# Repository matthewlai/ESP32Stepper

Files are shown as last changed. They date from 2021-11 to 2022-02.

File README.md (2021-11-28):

# ESP32Stepper

This is the PCB design and firmware for a Trinamic TMC2590-based stepper motor driver with an ESP32 microcontroller.

## Firmware Instructions

The firmware is Arduino based, using the arduino-esp32 port by Espressif.

1. Install the official Arduino IDE from [https://www.arduino.cc/en/software](https://www.arduino.cc/en/software).
2. [Install the ESP32 core](https://docs.espressif.com/projects/arduino-esp32/en/latest/installing.html) (either stable or development branch, using Board Manager).
3. Install the required libraries (see below) using Arduino library manager.
4. Clone this repository, and open ESP32Stepper/firmware/main/main.ino in the Arduino IDE.
5. In Tools, use the following settings:
    * Board: ESP32 Dev Module
    * Port: serial port for the board
    * All other settings as default (240 MHz CPU, 80 MHz flash, QIO, 4MB flash, default 4MB partition scheme, no PSRAM)

## Customisation

1. Set motor-specific parameters in config.h

## Required Libraries

1. Adafruit Neopixel 1.10.0x

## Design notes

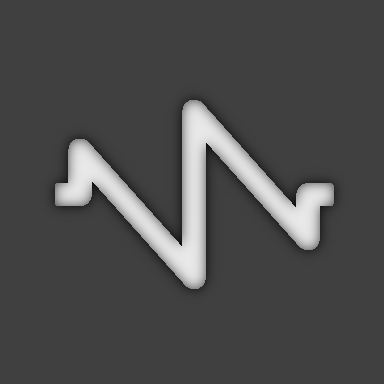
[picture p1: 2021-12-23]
controller/Woodpecker/qml/images/patterns/sawtooth.png

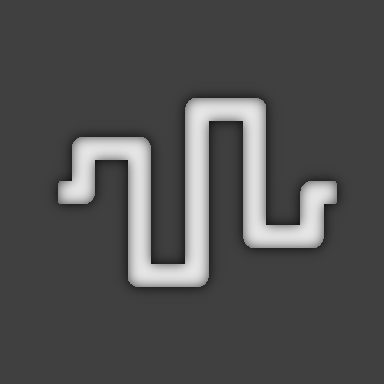
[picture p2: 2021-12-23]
controller/Woodpecker/qml/images/patterns/square.png

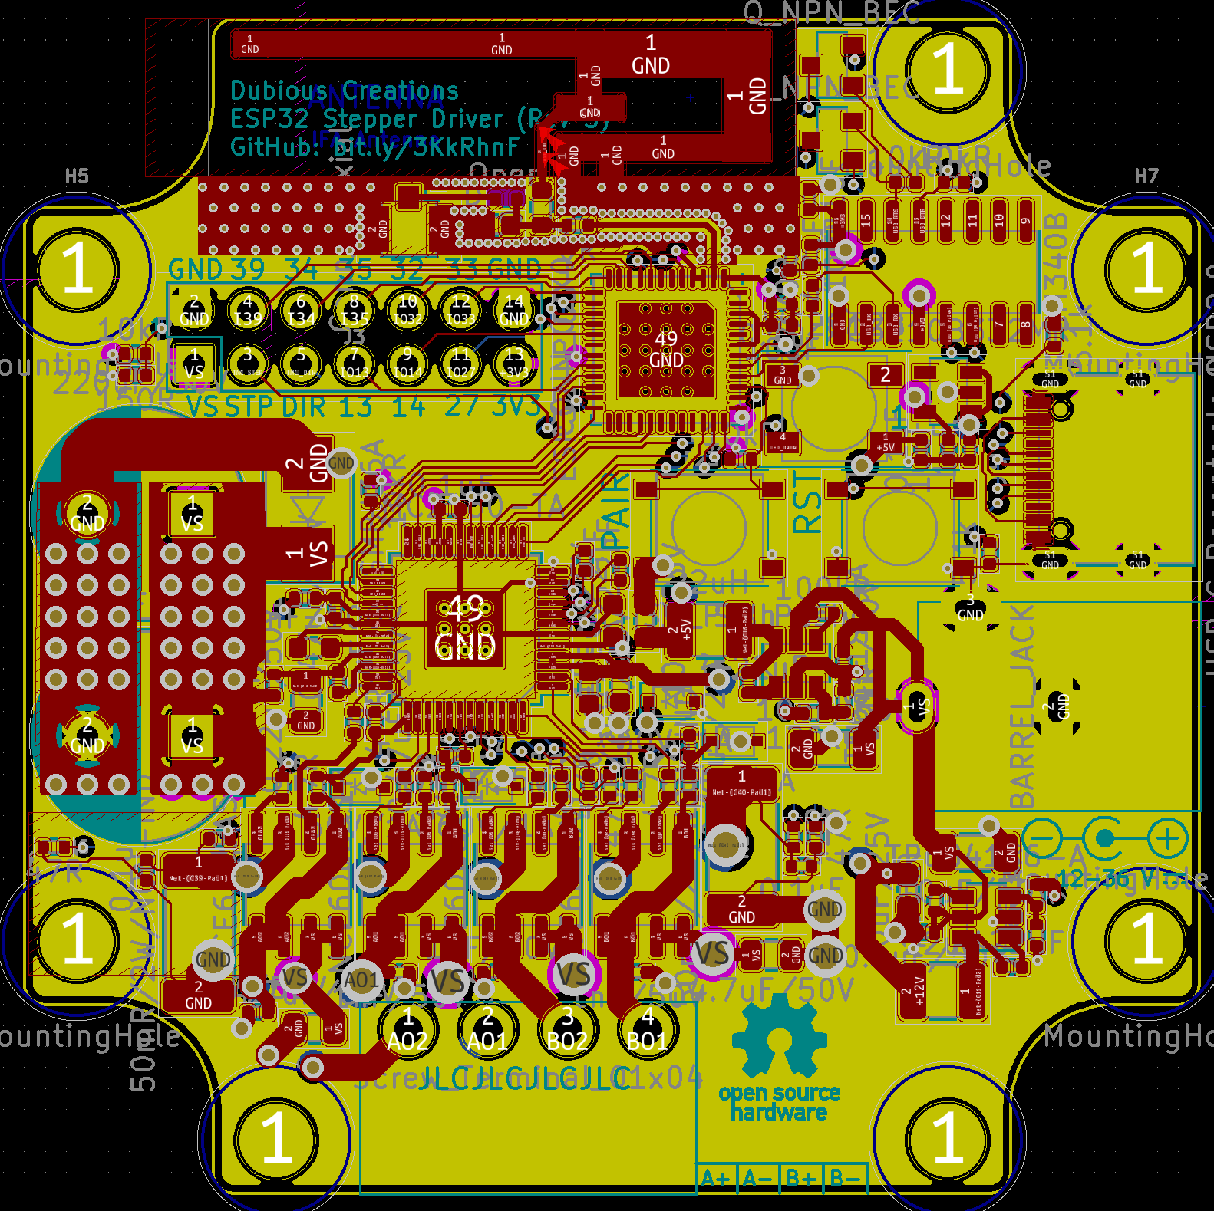
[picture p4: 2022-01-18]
doc/rev3/front.png

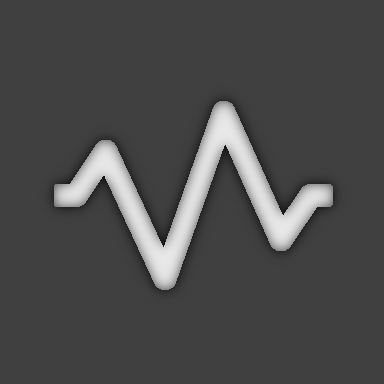
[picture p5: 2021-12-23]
controller/Woodpecker/qml/images/patterns/triangle.png

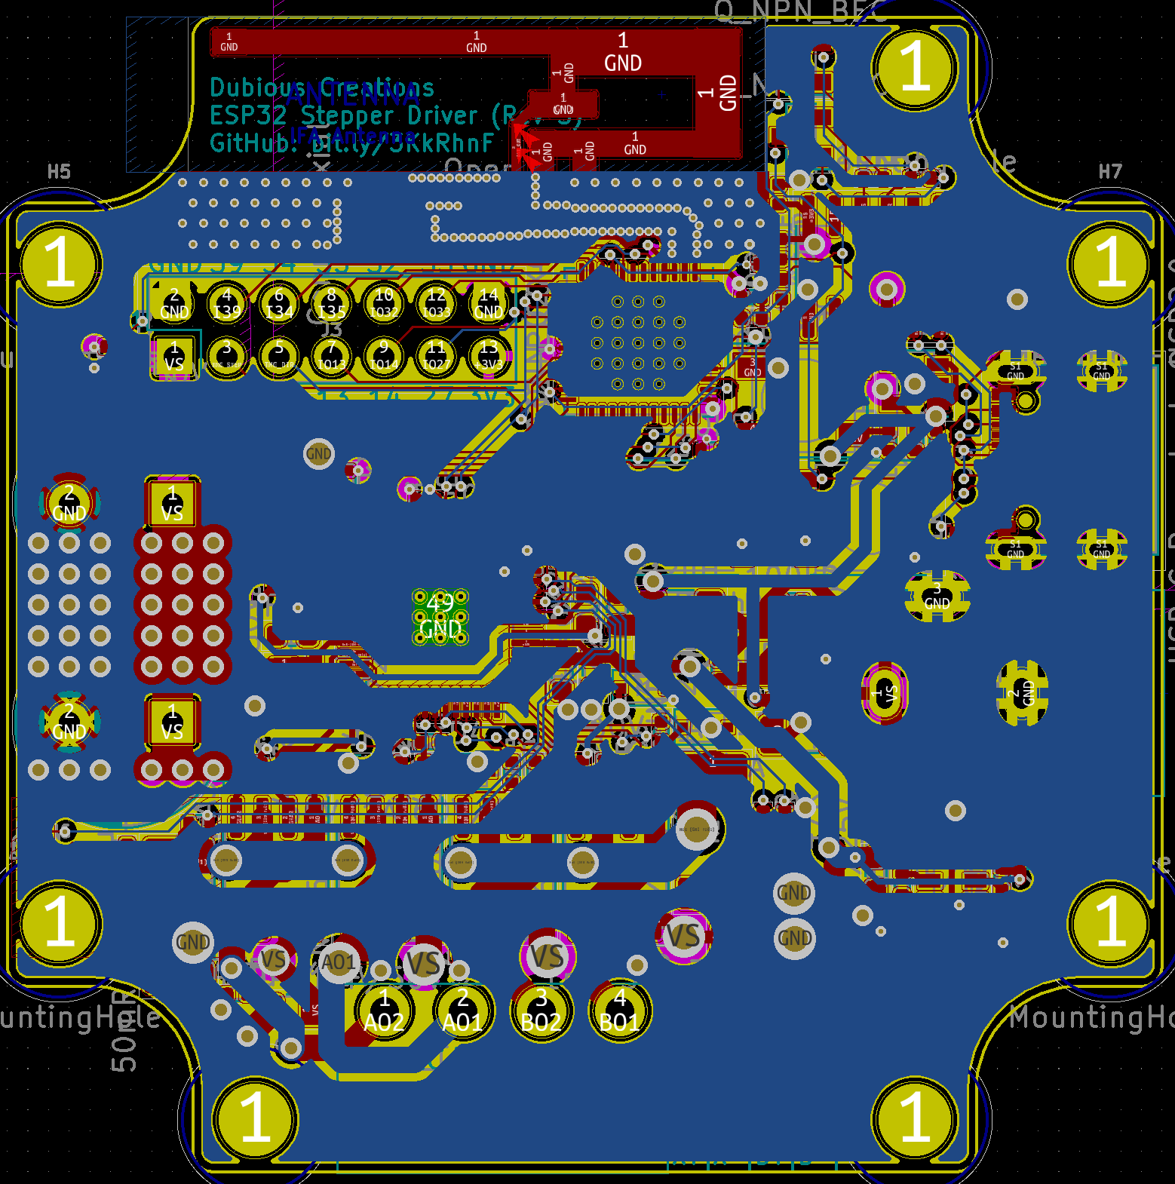
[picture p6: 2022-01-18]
doc/rev3/back.png

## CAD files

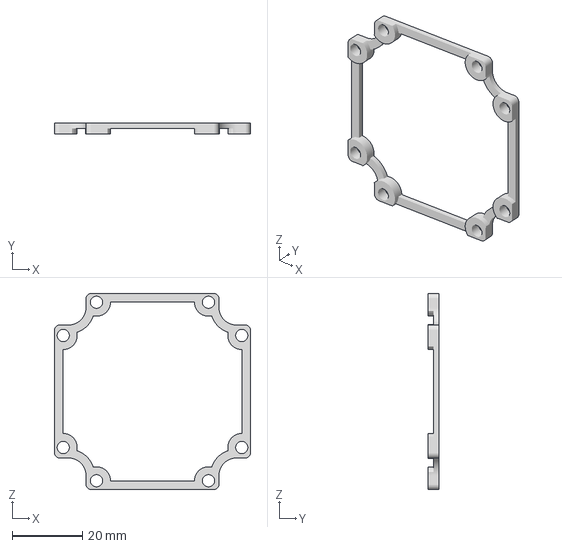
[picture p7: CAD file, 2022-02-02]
mechanical/NEMA23_Stepper_Spacer/stepper_spacer.3mf
56.0 x 3.00 x 56.0 mm

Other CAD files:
mechanical/NEMA23_Stepper_Spacer/stepper_spacer.f3d

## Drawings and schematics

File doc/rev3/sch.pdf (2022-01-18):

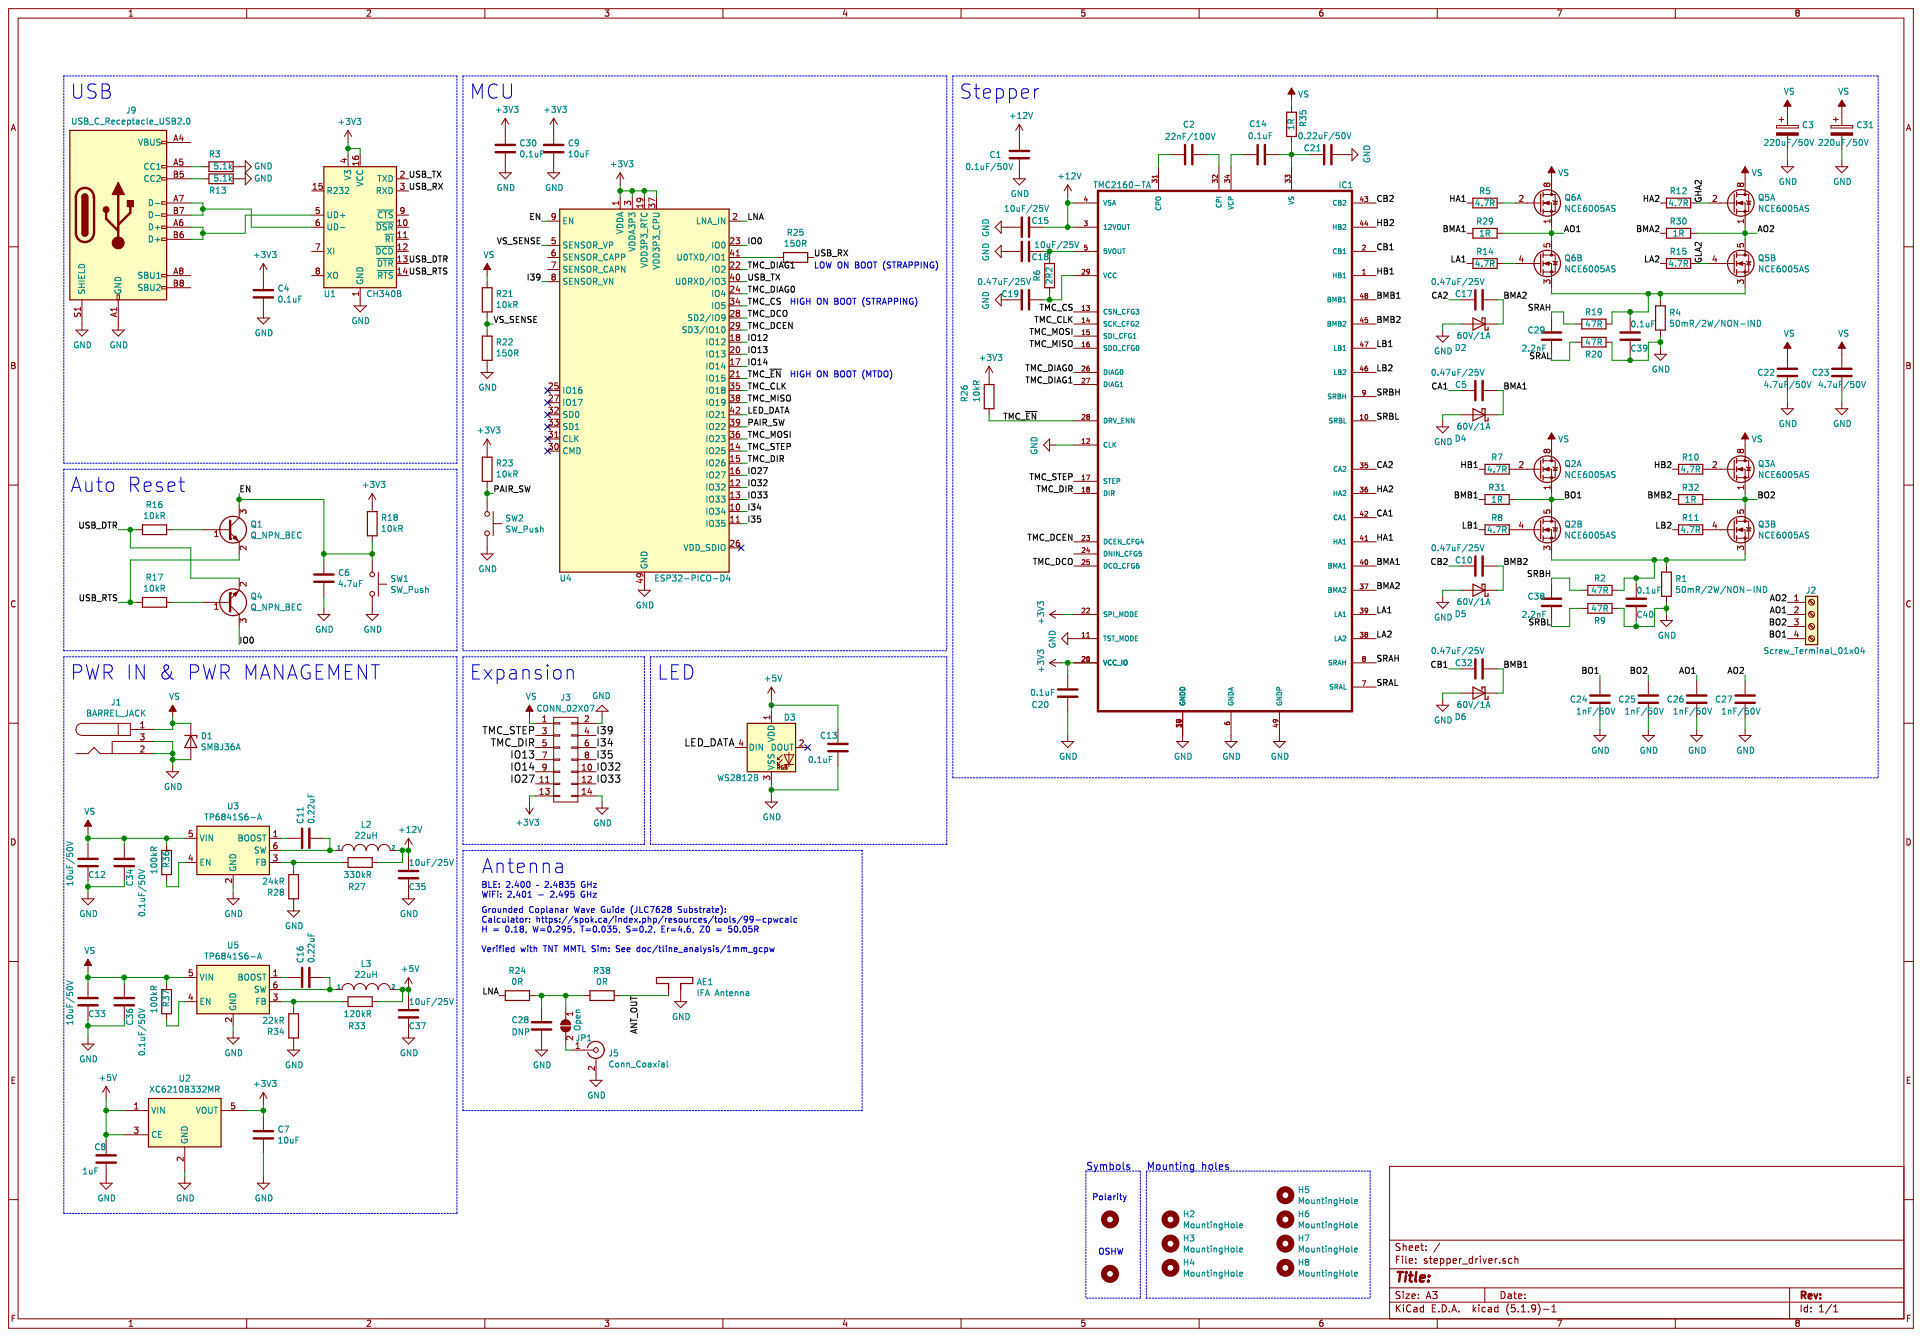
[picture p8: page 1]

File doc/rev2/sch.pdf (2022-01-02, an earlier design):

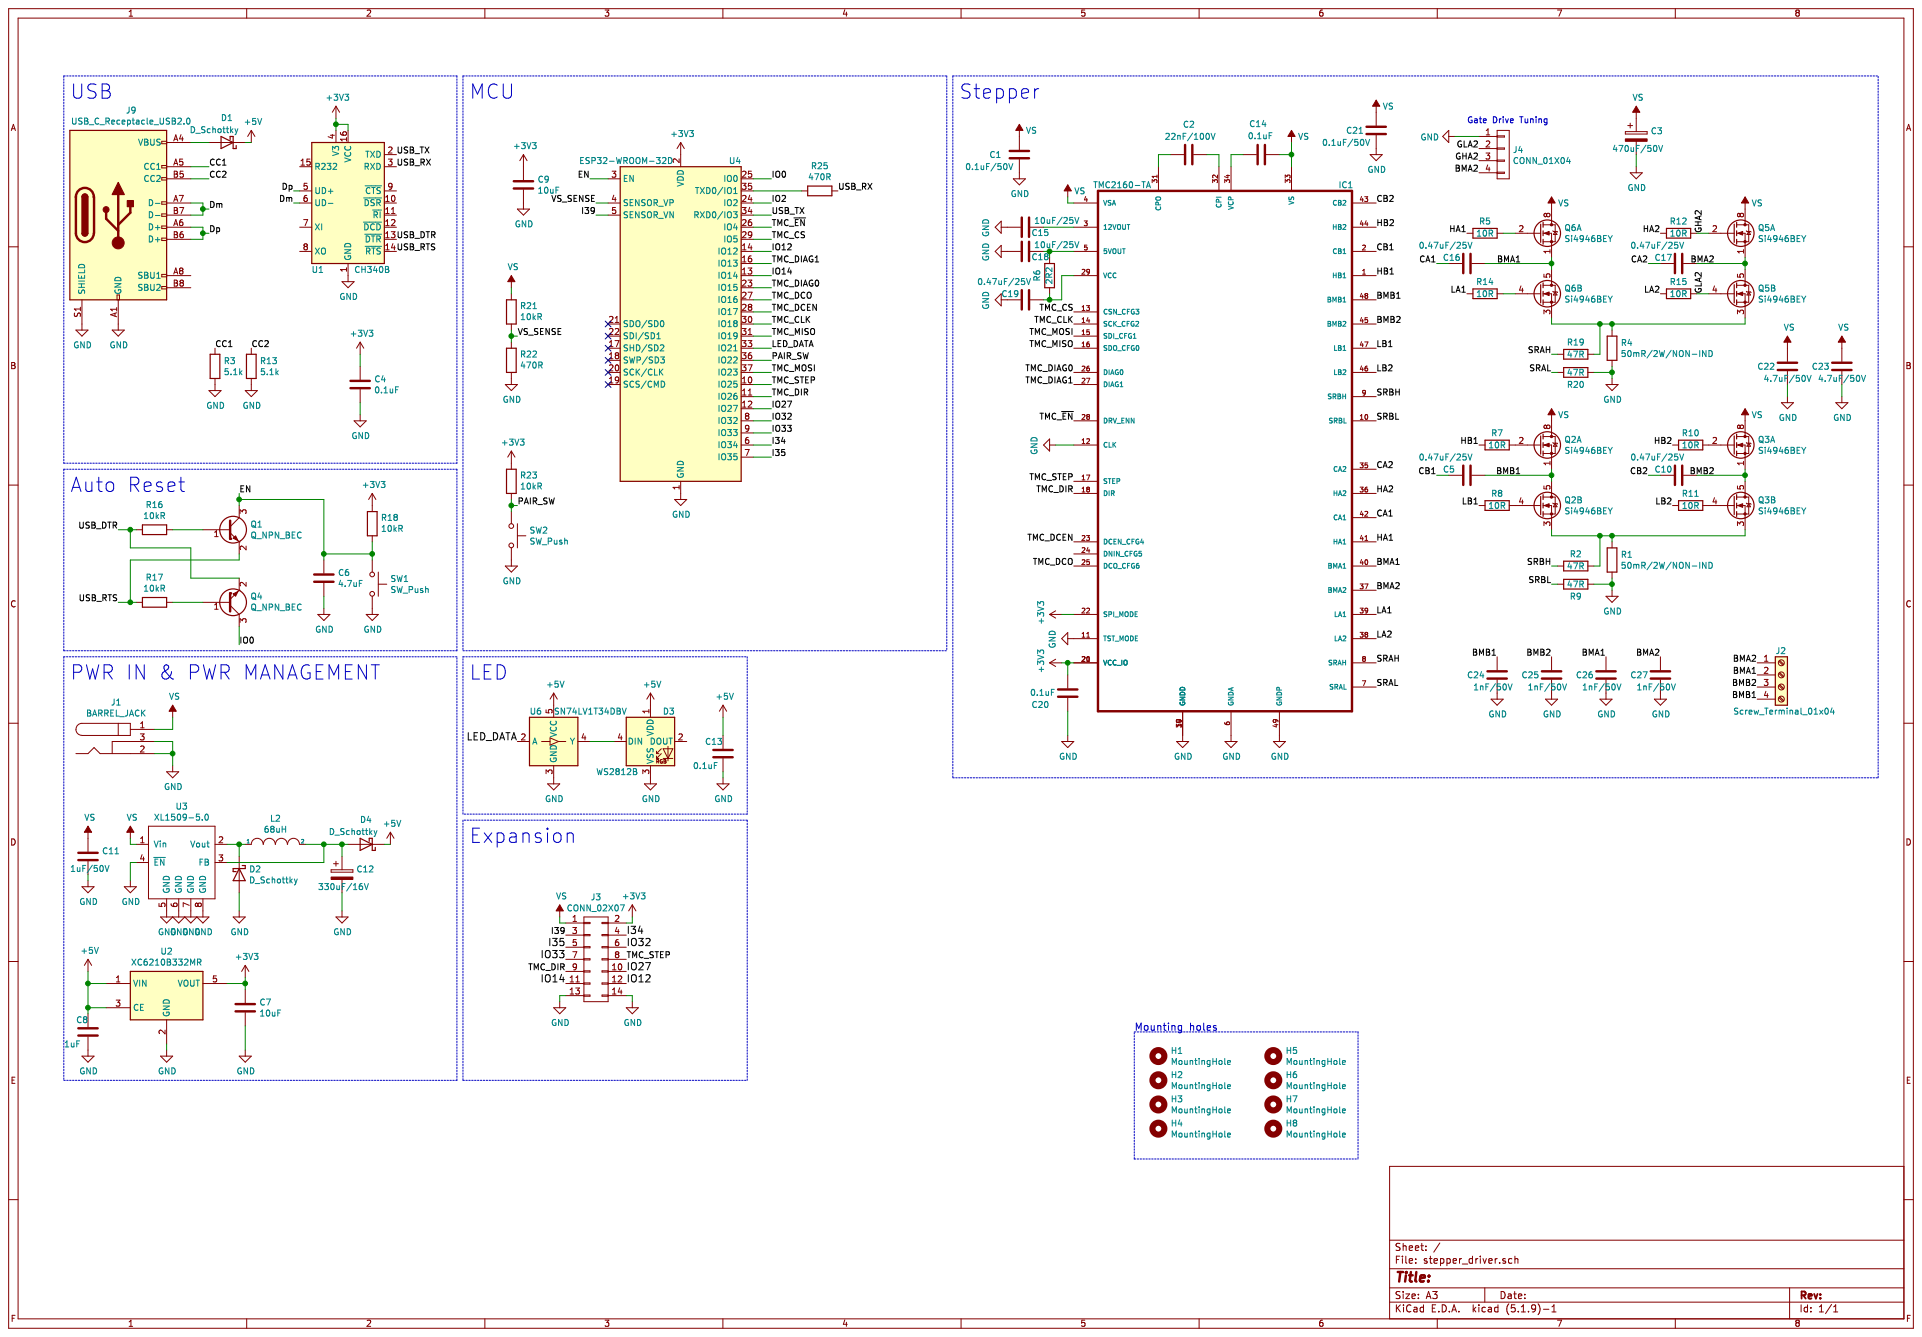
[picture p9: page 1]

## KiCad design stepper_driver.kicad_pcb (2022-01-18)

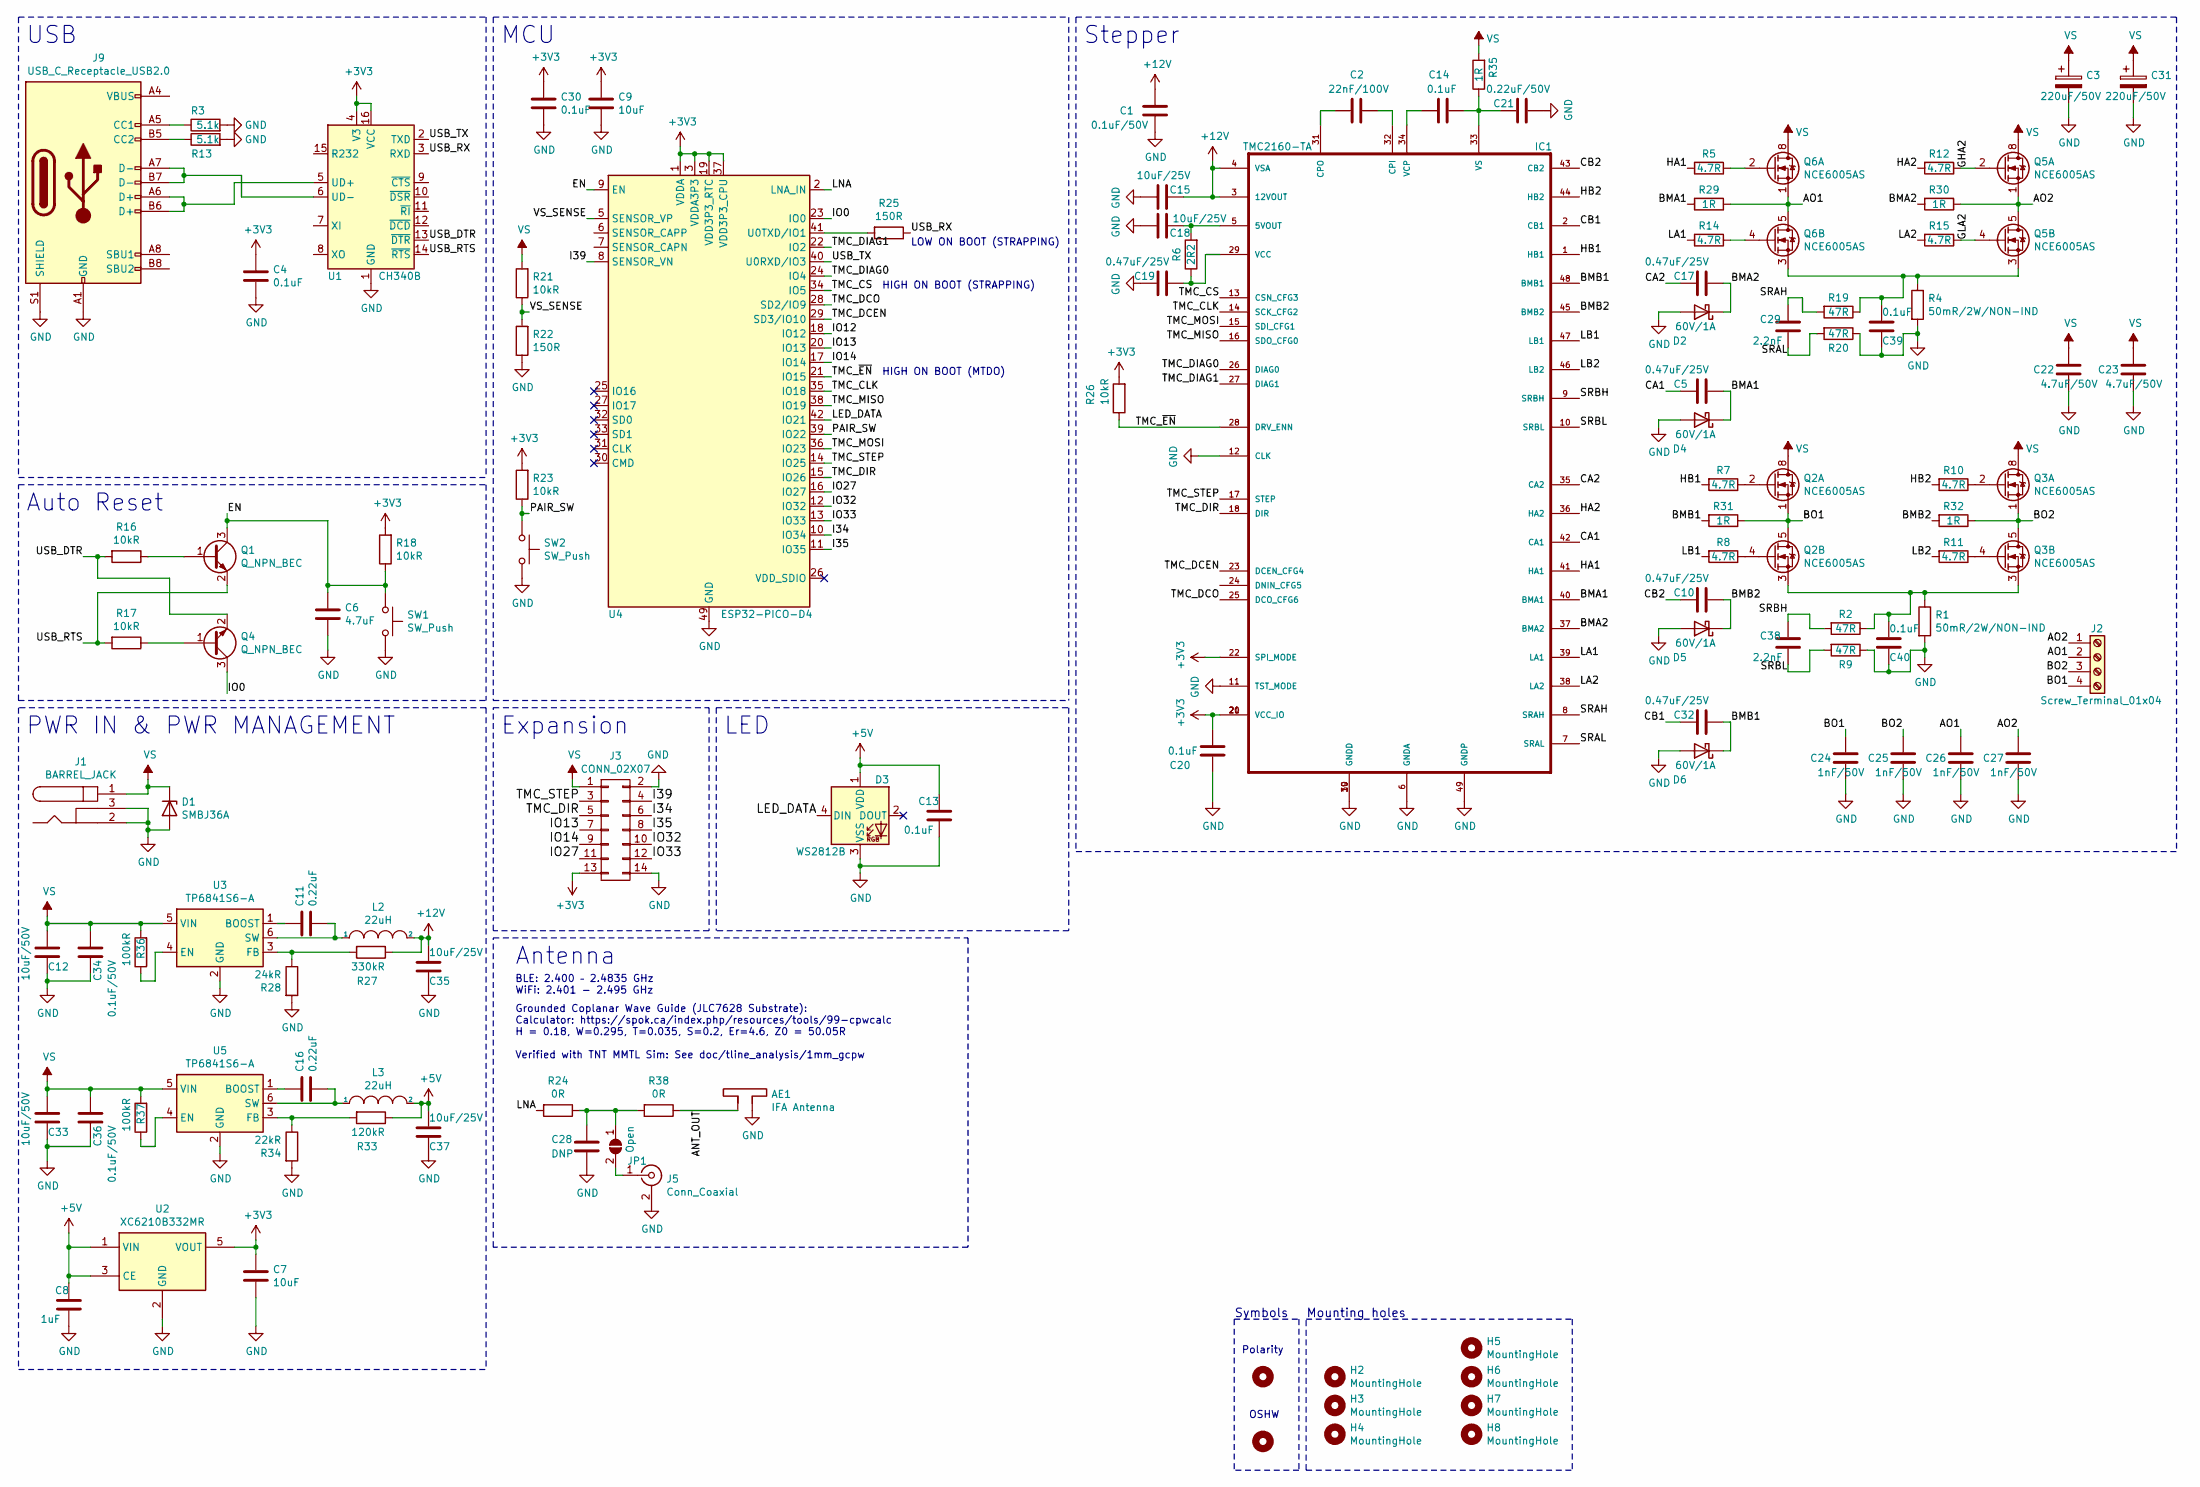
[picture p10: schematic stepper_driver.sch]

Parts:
AE1: IFA Antenna; TI_DN007_2.4GHz
C1: 0.1uF/50V; C_0603_1608Metric; LCSC C14663
C2: 22nF/100V; C_0603_1608Metric; LCSC C342519
C3, C31: 220uF/50V; CP_Radial_D10.0mm_P5.00mm; LCSC C88723
C4, C13, C14, C20, C30, C39, C40: 0.1uF; C_0402_1005Metric; LCSC C1525
C5, C10, C17, C19, C32: 0.47uF/25V; C_0402_1005Metric; LCSC C437527
C6: 4.7uF; C_0402_1005Metric; LCSC C23733
C7, C9: 10uF; C_0402_1005Metric; LCSC C15525
C8: 1uF; C_0402_1005Metric; LCSC C52923
C11, C16: 0.22uF; C_0402_1005Metric; LCSC C16772
C12, C33: 10uF/50V; C_1206_3216Metric; LCSC C13585
C15, C18, C35, C37: 10uF/25V; C_0603_1608Metric; LCSC C386081
C21: 0.22uF/50V; C_0805_2012Metric; LCSC C5378
C22, C23: 4.7uF/50V; C_0805_2012Metric; LCSC C162420
C24, C25, C26, C27: 1nF/50V; C_0402_1005Metric; LCSC C1523
C28: DNP; C_0603_1608Metric
C29, C38: 2.2nF; C_0402_1005Metric; LCSC C1531
C34, C36: 0.1uF/50V; C_0402_1005Metric; LCSC C307331
D1: SMBJ36A; D_SMB; LCSC C294880
D2, D4, D5, D6: 60V/1A; D_SOD-323F; LCSC C364278
D3: WS2812B; LED_WS2812B_PLCC4_5.0x5.0mm_P3.2mm; LCSC C2761795
H2, H3, H4, H5, H6, H7, H8: MountingHole; MountingHole_3.5mm
H9: MountingHole; Symbol_Barrel_Polarity
H10: MountingHole; OSHW-Logo_5.7x6mm_SilkScreen
IC1: TMC2160-TA; LQFP-48-1EP_7x7mm_P0.5mm_EP3.6x3.6mm_ThermalVias; LCSC C465948
J1: BARREL_JACK; DC-005C-25A; LCSC C223903
J2: Screw_Terminal_01x04; KF2EDGR-3.81-4P; LCSC C441184
J3: CONN_02X07; PinHeader_2x07_P2.54mm_Vertical
J5: Conn_Coaxial; U.FL_Hirose_U.FL-R-SMT-1_Vertical; LCSC C88374
J9: USB_C_Receptacle_USB2.0; USB_C_Receptacle_XKB_U262-16XN-4BVC11; LCSC C319148
JP1: Open; R_0402_1005Metric
L2, L3: 22uH; L_1210_3225Metric; LCSC C223225
Q1, Q4: Q_NPN_BEC; SOT-23; LCSC C2150
Q2, Q3, Q5, Q6: NCE6005AS; SOIC-8_3.9x4.9mm_P1.27mm; LCSC C126151
R1, R4: 50mR/2W/NON-IND; R_2512_6332Metric_Pad1.52x3.35mm_HandSolder; LCSC C160588
R2, R9, R19, R20: 47R; R_0402_1005Metric; LCSC C25118
R3, R13: 5.1k; R_0402_1005Metric; LCSC C25905
R5, R7, R8, R10, R11, R12, R14, R15: 4.7R; R_0402_1005Metric; LCSC C25121
R6: 2R2; R_0402_1005Metric; LCSC C25158
R16, R17, R18, R21, R23, R26: 10kR; R_0402_1005Metric; LCSC C25744
R22, R25: 150R; R_0402_1005Metric; LCSC C25082
R24: 0R; R_0402_1005Metric; LCSC C17168
R27: 330kR; R_0402_1005Metric; LCSC C25778
R28: 24kR; R_0402_1005Metric; LCSC C25769
R29, R30, R31, R32, R35: 1R; R_0402_1005Metric; LCSC C25086
R33: 120kR; R_0402_1005Metric; LCSC C25750
R34: 22kR; R_0402_1005Metric; LCSC C25768
R36, R37: 100kR; R_0402_1005Metric; LCSC C25741
R38: 0R; R_0603_1608Metric; LCSC C21189
SW1, SW2: SW_Push; SW_Push_1P1T_NO_5.1x5.1mm; LCSC C318887
U1: CH340B; SOIC-16_3.9x9.9mm_P1.27mm; LCSC C81010
U2: XC6210B332MR; SOT-23-5; LCSC C47719
U3, U5: TP6841S6-A; SOT-23-6; LCSC C2844924
U4: ESP32-PICO-D4; LCSC C193707

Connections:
+3V3: C4.1, C7.1, C9.1, C20.2, C30.1, IC1.20 (VCC_IO), IC1.21 (VCC_IO), IC1.22 (SPI_MODE), J3.13, R18.2, R23.2, R26.2, U1.4 (V3), U1.16 (VCC), U2.5 (VOUT), U4.1 (VDDA), U4.3 (VDDA3P3), U4.4 (VDDA3P3), U4.19 (VDD3P3_RTC), U4.37 (VDD3P3_CPU), U4.43 (VDDA), U4.46 (VDDA)
+5V: C8.1, C13.1, C37.1, D3.1 (VDD), L3.2, R33.1, U2.1 (VIN), U2.3 (CE)
+12V: C1.1, C15.2, C35.1, IC1.3 (12VOUT), IC1.4 (VSA), L2.2, R27.1
/ANT_OUT: AE1.2, R38.1
/AO1: C26.1, J2.2, Q6.1 (S1), Q6.5 (D2), Q6.6 (D2), R29.1
/AO2: C27.1, J2.1, Q5.1 (S1), Q5.5 (D2), Q5.6 (D2), R30.1
/BMA1: C5.1, D4.1 (K), IC1.40 (BMA1), R29.2
/BMA2: C17.1, D2.1 (K), IC1.37 (BMA2), R30.2
/BMB1: C32.1, D6.1 (K), IC1.48 (BMB1), R31.2
/BMB2: C10.1, D5.1 (K), IC1.45 (BMB2), R32.2
/BO1: C24.1, J2.4, Q2.1 (S1), Q2.5 (D2), Q2.6 (D2), R31.1
/BO2: C25.1, J2.3, Q3.1 (S1), Q3.5 (D2), Q3.6 (D2), R32.1
/CA1: C5.2, IC1.42 (CA1)
/CA2: C17.2, IC1.35 (CA2)
/CB1: C32.2, IC1.2 (CB1)
/CB2: C10.2, IC1.43 (CB2)
/EN: C6.1, Q1.3 (C), R18.1, SW1.1, U4.9 (EN)
/GHA2: Q5.2 (G1), R12.1
/GLA2: Q5.4 (G2), R15.1
/HA1: IC1.41 (HA1), R5.2
/HA2: IC1.36 (HA2), R12.2
/HB1: IC1.1 (HB1), R7.2
/HB2: IC1.44 (HB2), R10.2
/I34: J3.6, U4.10 (IO34)
/I35: J3.8, U4.11 (IO35)
/I39: J3.4, U4.8 (SENSOR_VN)
/IO0: Q4.3 (C), U4.23 (IO0)
/IO13: J3.7, U4.20 (IO13)
/IO14: J3.9, U4.17 (IO14)
/IO27: J3.11, U4.16 (IO27)
/IO32: J3.10, U4.12 (IO32)
/IO33: J3.12, U4.13 (IO33)
/LA1: IC1.39 (LA1), R14.2
/LA2: IC1.38 (LA2), R15.2
/LB1: IC1.47 (LB1), R8.2
/LB2: IC1.46 (LB2), R11.2
/LED_DATA: D3.4 (DIN), U4.42 (IO21)
/LNA: R24.2, U4.2 (LNA_IN)
/PAIR_SW: R23.1, SW2.1, U4.39 (IO22)
/SRAH: C29.1, IC1.8 (SRAH), R19.2
/SRAL: C29.2, IC1.7 (SRAL), R20.2
/SRBH: C38.1, IC1.9 (SRBH), R2.2
/SRBL: C38.2, IC1.10 (SRBL), R9.2
/TMC_CLK: IC1.14 (SCK_CFG2), U4.35 (IO18)
/TMC_CS: IC1.13 (CSN_CFG3), U4.34 (IO5)
/TMC_DCEN: IC1.23 (DCEN_CFG4), U4.29 (SD3/IO10)
/TMC_DCO: IC1.25 (DCO_CFG6), U4.28 (SD2/IO9)
/TMC_DIAG0: IC1.26 (DIAG0), U4.24 (IO4)
/TMC_DIAG1: IC1.27 (DIAG1), U4.22 (IO2)
/TMC_DIR: IC1.18 (DIR), J3.5, U4.15 (IO26)
/TMC_MISO: IC1.16 (SDO_CFG0), U4.38 (IO19)
/TMC_MOSI: IC1.15 (SDI_CFG1), U4.36 (IO23)
/TMC_STEP: IC1.17 (STEP), J3.3, U4.14 (IO25)
/TMC_~EN: IC1.28 (DRV_ENN), R26.1, U4.21 (IO15)
/USB_DTR: Q4.2 (E), R16.2, U1.13 (~DTR)
/USB_RTS: Q1.2 (E), R17.2, U1.14 (~RTS)
/USB_RX: R25.1, U1.3 (RXD)
/USB_TX: U1.2 (TXD), U4.40 (U0RXD/IO3)
/VS_SENSE: R21.1, R22.2, U4.5 (SENSOR_VP)
GND: AE1.1, C1.2, C3.2, C4.2, C6.2, C7.2, C8.2, C9.2, C12.2, C13.2, C15.1, C18.1, C19.2, C20.1, C21.2, C22.2, C23.2, C24.2, C25.2, C26.2, C27.2, C28.2, C30.2, C31.2, C33.2, C34.1, C35.2, C36.1, C37.2, C39.2, C40.2, D1.2 (A), D2.2 (A), D3.3 (VSS), D4.2 (A), D5.2 (A), D6.2 (A), IC1.6 (GNDA), IC1.11 (TST_MODE), IC1.12 (CLK), IC1.19 (GNDD), IC1.30 (GNDD), IC1.49 (GNDP), J1.2, J1.3, J3.2, J3.14, J5.2 (Ext), J9.A1 (GND), J9.A12 (GND), J9.B1 (GND), J9.B12 (GND), J9.S1 (SHIELD), R1.2, R3.2, R4.2, R9.1, R13.2, R20.1, R22.1, R28.2, R34.2, SW1.2, SW2.2, U1.1 (GND), U2.2 (GND), U3.2 (GND), U4.49 (GND), U5.2 (GND)
unnamed: C2.1, IC1.32 (CPI)
unnamed: C2.2, IC1.31 (CPO)
unnamed: C11.1, U3.1 (BOOST)
unnamed: C11.2, L2.1, U3.6 (SW)
unnamed: C14.1, IC1.34 (VCP)
unnamed: C14.2, C21.1, IC1.33 (VS), R35.1
unnamed: C16.1, U5.1 (BOOST)
unnamed: C16.2, L3.1, U5.6 (SW)
unnamed: C18.2, IC1.5 (5VOUT), R6.2
unnamed: C19.1, IC1.29 (VCC), R6.1
unnamed: C28.1, JP1.1 (A), R24.1, R38.2
unnamed: C39.1, Q5.3 (S2), Q6.3 (S2), R4.1, R19.1
unnamed: C40.1, Q2.3 (S2), Q3.3 (S2), R1.1, R2.1
unnamed: J5.1 (In), JP1.2 (B)
unnamed: J9.A4 (VBUS), J9.A9 (VBUS), J9.B4 (VBUS), J9.B9 (VBUS)
unnamed: J9.A5 (CC1), R3.1
unnamed: J9.A6 (D+), J9.B6 (D+), U1.5 (UD+)
unnamed: J9.A7 (D-), J9.B7 (D-), U1.6 (UD-)
unnamed: J9.B5 (CC2), R13.1
unnamed: Q1.1 (B), R16.1
unnamed: Q2.2 (G1), R7.1
unnamed: Q2.4 (G2), R8.1
unnamed: Q3.2 (G1), R10.1
unnamed: Q3.4 (G2), R11.1
unnamed: Q4.1 (B), R17.1
unnamed: Q6.2 (G1), R5.1
unnamed: Q6.4 (G2), R14.1
unnamed: R25.2, U4.41 (U0TXD/IO1)
unnamed: R27.2, R28.1, U3.3 (FB)
unnamed: R33.2, R34.1, U5.3 (FB)
unnamed: R36.1, U3.4 (EN)
unnamed: R37.1, U5.4 (EN)
VS: C3.1, C12.1, C22.1, C23.1, C31.1, C33.1, C34.2, C36.2, D1.1 (K), J1.1, J3.1, Q2.7 (D1), Q2.8 (D1), Q3.7 (D1), Q3.8 (D1), Q5.7 (D1), Q5.8 (D1), Q6.7 (D1), Q6.8 (D1), R21.2, R35.2, R36.2, R37.2, U3.5 (VIN), U5.5 (VIN)

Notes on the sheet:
Mounting holes
USB
Auto Reset
MCU
LED
PWR IN & PWR MANAGEMENT
Expansion
Stepper
Antenna
BLE: 2.400 – 2.4835 GHz WiFi: 2.401 - 2.495 GHz
Grounded Coplanar Wave Guide (JLC7628 Substrate): Calculator: https://spok.ca/index.php/resources/tools/99-cpwcalc H = 0.18, W=0.295, T=0.035, S=0.2, Er=4.6, Z0 = 50.05R Verified with TNT MMTL Sim: See doc/tline_analysis/1mm_gcpw
Symbols
Polarity
OSHW
HIGH ON BOOT (STRAPPING)
HIGH ON BOOT (MTDO)
LOW ON BOOT (STRAPPING)

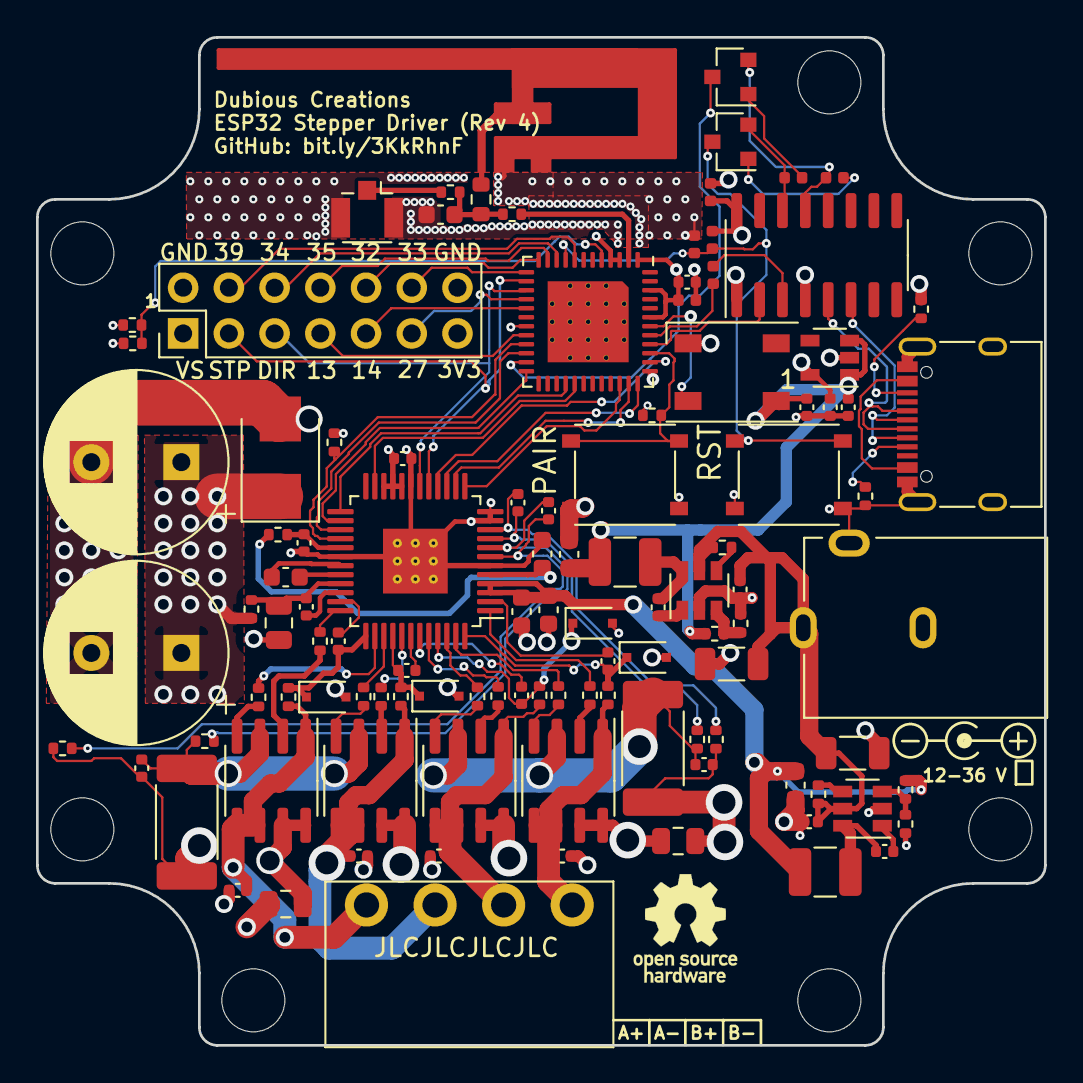
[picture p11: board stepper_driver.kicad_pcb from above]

Board: 4 copper layers, 56.0 x 56.0 mm, 116 parts (0 on the bottom side), 93 nets.

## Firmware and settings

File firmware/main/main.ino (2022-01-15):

// Libraries:
// Adafruit Neopixel 1.10.0x

#include <Adafruit_NeoPixel.h>

#include <SPI.h>

#include "ble.h"
#include "config.h"
#include "crash.h"
#include "delay_inserter.h"
#include "homing_controller.h"
#include "stepper_control.h"

// Globals --------------------------------------------------------
Adafruit_NeoPixel g_rgb_led(/*count=*/1, kLedData);

MotionController g_motion_controller;
// ----------------------------------------------------------------

// Example Motion Update Commands ---------------------------------

void MoveToMiddle(MotionController* motion_controller, int32_t range) {
  int32_t target = range * 0.5f;
  if (fabs(motion_controller->GetCurrentPosition() - target) > kPositionTolerance * range) {
    motion_controller->UpdateTargetSpeedByPosition(target, kMaxSpeed);
  } else {
    motion_controller->SetTargetSpeed(0.0f);
  }
}

void MoveAtConstantSpeed(MotionController* motion_controller, float v) {
  motion_controller->SetTargetSpeed(v);
}

// Oscillate as fast as possible between x1 and x2 positions.
void Oscillate(MotionController* motion_controller, int32_t range, int32_t x1, int32_t x2) {
  static int32_t current_target = x1;
  auto current_position = motion_controller->GetCurrentPosition();
  if (fabs(current_position - current_target) < kPositionTolerance * range) {
    float dist_to_x1 = fabs(current_position - x1);
    float dist_to_x2 = fabs(current_position - x2);
    if (dist_to_x1 > dist_to_x2) {
      current_target = x1;
    } else {
      current_target = x2;
    }
  }
  motion_controller->UpdateTargetSpeedByPosition(current_target, kMaxSpeed);
}

// Time based velocity oscillation without homing.
void Oscillate(MotionController* motion_controller, float v, float period_s) {
  float time_now = float(micros()) / 1000000.0f;
  float scale = sin(2.0f * 3.14f / period_s * time_now);
  motion_controller->SetTargetSpeed(v * scale);
}

// Switching direction as fast as possible.
void AbruptOscillate(MotionController* motion_controller, float v, float period_s) {
  float time_now = float(micros()) / 1000000.0f;
  float mod = fmod(time_now, period_s);
  float dir = (mod > (period_s / 2)) ? 1.0f : -1.0f;
  motion_controller->SetTargetSpeed(dir * v);
}

// ----------------------------------------------------------------

void SetRGBLedColour(float r, float g, float b) {
  static int last_r = 0;
  static int last_g = 0;
  static int last_b = 0;
  int new_r = int(r * 255);
  int new_g = int(g * 255);
  int new_b = int(b * 255);
  if (last_r != new_r || last_g != new_g || last_b != new_b) {
    g_rgb_led.setPixelColor(0, int(r * 255), int(g * 255), int(b * 255));
    g_rgb_led.show();
    last_r = new_r;
    last_g = new_g;
    last_b = new_b;
  }
}

void CrashHandler(const String& msg) {
  g_motion_controller.Stop();
  for (;;) {
    Serial.println(msg);
    SetRGBLedColour(0.1f, 0.0f, 0.0f);
    delay(500);
    SetRGBLedColour(0.0f, 0.0f, 0.0f);
    delay(500);
  }
}

void setup() {
  pinMode(kLedData, OUTPUT);

  #ifdef HAS_PAIR_SWITCH
  pinMode(kPairSw, INPUT);
  #endif
  
  g_rgb_led.begin();
  Serial.begin(115200);

  delay(100);

  Serial.println("Setting up");

  g_motion_controller.Begin();
}

void loop() {
  auto t = millis();

  #ifdef HAS_PAIR_SWITCH
  if (digitalRead(kPairSw) == LOW) {
    g_motion_controller.Stop();
    for (;;) {}
  }
  #endif

  #ifdef HAS_VSENSE
  // Over-voltage check
  float vs = analogReadMilliVolts(kVSenseADCPin) / 1000.0f * kVSenseScale;
  if (vs > kVsOvervoltageThreshold) {
    CRASH_AND_BURN(String("VS Over-voltage detected! VS=") + String(vs) + "V");
  }
  #endif

  constexpr float kPeriodMs = 1000.0f;
  constexpr float kBrightness = 0.1f;
  constexpr float kCoeff = (2 * M_PI) / kPeriodMs;
  float r = sin(kCoeff * t) * 0.5f + 0.5f;
  float g = sin(kCoeff * t + (0.33f * 2.0f * M_PI)) * 0.5f + 0.5f;
  float b = sin(kCoeff * t + (0.66f * 2.0f * M_PI)) * 0.5f + 0.5f;
  SetRGBLedColour(kBrightness * r, kBrightness * g, kBrightness * b);

  static WoodpeckerBLEServer ble_server;

  static bool last_run_setting = false;
  bool run_setting = ble_server.Started();

  if (last_run_setting != run_setting) {
    Serial.print("Started=");
    Serial.println(run_setting);
    last_run_setting = run_setting;
  }

  static HomingController homing_controller(&g_motion_controller);

  if (kUseStallGuardHoming && !homing_controller.Done()) {
    homing_controller.Update();
  } else {
    Oscillate(&g_motion_controller, homing_controller.Range(), homing_controller.Range() * 0.3f, homing_controller.Range() * 0.7f);
    //MoveToMiddle(&g_motion_controller, homing_controller.Range());
    //MoveAtConstantSpeed(&g_motion_controller, 60.0f);
    //Oscillate(&g_motion_controller, kMaxSpeed, 2.0f);
    //AbruptOscillate(&g_motion_controller, kMaxSpeed, 5.0f);
  }

  // Run the control loop at approx 200 Hz.
  // This is only for velocity updates. Stepping happens asynchronously.
  // We put the delay inserter here because this is the most crucial part
  // for loop timing.
  static DelayInserter<5000> delay_inserter;
  delay_inserter.Sync();
  g_motion_controller.Update();
}

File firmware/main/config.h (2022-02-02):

#ifndef CONFIG_H
#define CONFIG_H

// Board selection ------------------------------------------------------------

// Uncomment one of the following:

// First revision boards with TMC2590
//#define HW_REV 1

// Second revision boards with TMC2160(A)
//#define HW_REV 2

// Third revision boards with TMC2160(A) and ESP32-PICO-D4
#define HW_REV 3

// ----------------------------------------------------------------------------

// Stepper config -------------------------------------------------------------
// Motor current limit in Amps(rms). Maximum supported by this board is 4.6A.
// The driver will never exceed this limit.
constexpr float kMotorCurrentLimit = 1.6f;

// Flip all directions.
constexpr bool kFlipDrivingDirection = false;

constexpr int kFullStepsPerRev = 200;

// Maximum speed in Revs/s.
constexpr float kMaxSpeed = 13.3f; // 800 RPM

// Maximum acceleration in Revs/s^2.
constexpr float kMaxAcceleration = 500.0f;

// Maximum jerk in Rev/s^3
constexpr float kMaxJerk = 10000.0f;

constexpr float kHomingSpeedRPM = 100.0f;
constexpr float kHomingCurrent = 0.6f;
constexpr float kHomingAcceleration = 50.0f;

// Effectively disable max jerk limit during homing, so we don't try
// driving hard into the end.
constexpr float kHomingMaxJerk = 1000000.0f;

// StallGuard 2 sensitivity setting. See 5. StallGuard2 Load Measurement in
// the datasheet. Higher values = less sensitive. (63 to -64).
// Value per direcion [forward, backward].
constexpr int8_t kStallGuardThreshold[2] = { 3, 0 };

// StallGuard doesn't work at very low velocities due to weak back-emf.
// This is the speed in Rev/s below which StallGuard should not be trusted.
// On TMC2160 this is done automatically on the driver side with TCOOLTHRS.
// 1 RPS should work for most motors, but may need to be higher for motors
// smaller than NEMA17.
constexpr float kStallGuardMinSpeed = 1.0f;

// ----------------------------------------------------------------------------

// Motion planning config -----------------------------------------------------
constexpr bool kUseStallGuardHoming = true;

// Position controller will consider target reached when we get this close to
// target position as a fraction of total range.
constexpr float kPositionTolerance = 0.01f;

// Velocities below this (Rev/s) are ignored by the driver (assumed to be
// rounding errors).
constexpr float kMinVelocity = 0.0001f;

// ----------------------------------------------------------------------------

// Program config -------------------------------------------------------------

// Output all stepper / trajectory parameters at each control step for plotting.
// (Can cause step skipping due to the volume of data printed).
constexpr bool kStepperDebugPlotting = false;

// ----------------------------------------------------------------------------

// Board definitions ----------------------------------------------------------
#if HW_REV == 1
#define TMC2590
#else
#define TMC2160
#endif

#if HW_REV == 1

constexpr int kLedData = 21;

constexpr int kTmcEn = 4;
constexpr int kTmcStep = 25;
constexpr int kTmcDir = 26;
constexpr int kTmcSgTst = 27;

#elif HW_REV == 2

constexpr int kLedData = 21;

// Second revision has pair switch (currently used for stopping the driver).
#define HAS_PAIR_SWITCH
constexpr int kPairSw = 22;

#define HAS_VSENSE
constexpr int kVSenseADCPin = 36;
constexpr float kVSenseScale = (10000.0f + 470.0f) / 470.0f;
constexpr float kVsOvervoltageThreshold = 38.0f;

constexpr int kTmcEn = 4;
constexpr int kTmcStep = 25;
constexpr int kTmcDir = 26;

constexpr int kTmcDiag0 = 15;
constexpr int kTmcDiag1 = 13;

constexpr int kTmcDco = 16;
constexpr int kTmcDcEn = 17;

#elif HW_REV == 3

constexpr int kLedData = 21;

// Second revision has pair switch (currently used for stopping the driver).
#define HAS_PAIR_SWITCH
constexpr int kPairSw = 22;

#define HAS_VSENSE
constexpr int kVSenseADCPin = 36;
constexpr float kVSenseScale = (10000.0f + 150.0f) / 150.0f;
constexpr float kVsOvervoltageThreshold = 38.0f;

constexpr int kTmcEn = 15;
constexpr int kTmcStep = 25;
constexpr int kTmcDir = 26;

constexpr int kTmcDiag0 = 4;
constexpr int kTmcDiag1 = 2;

constexpr int kTmcDco = 9;
constexpr int kTmcDcEn = 10;

#endif

// ----------------------------------------------------------------------------

#endif  // CONFIG_H

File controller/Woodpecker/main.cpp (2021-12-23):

/***************************************************************************
**
** Copyright (C) 2017 The Qt Company Ltd.
** Contact: https://www.qt.io/licensing/
**
** This file is part of the examples of the QtBluetooth module of the Qt Toolkit.
**
** $QT_BEGIN_LICENSE:BSD$
** Commercial License Usage
** Licensees holding valid commercial Qt licenses may use this file in
** accordance with the commercial license agreement provided with the
** Software or, alternatively, in accordance with the terms contained in
** a written agreement between you and The Qt Company. For licensing terms
** and conditions see https://www.qt.io/terms-conditions. For further
** information use the contact form at https://www.qt.io/contact-us.
**
** BSD License Usage
** Alternatively, you may use this file under the terms of the BSD license
** as follows:
**
** "Redistribution and use in source and binary forms, with or without
** modification, are permitted provided that the following conditions are
** met:
**   * Redistributions of source code must retain the above copyright
**     notice, this list of conditions and the following disclaimer.
**   * Redistributions in binary form must reproduce the above copyright
**     notice, this list of conditions and the following disclaimer in
**     the documentation and/or other materials provided with the
**     distribution.
**   * Neither the name of The Qt Company Ltd nor the names of its
**     contributors may be used to endorse or promote products derived
**     from this software without specific prior written permission.
**
**
** THIS SOFTWARE IS PROVIDED BY THE COPYRIGHT HOLDERS AND CONTRIBUTORS
** "AS IS" AND ANY EXPRESS OR IMPLIED WARRANTIES, INCLUDING, BUT NOT
** LIMITED TO, THE IMPLIED WARRANTIES OF MERCHANTABILITY AND FITNESS FOR
** A PARTICULAR PURPOSE ARE DISCLAIMED. IN NO EVENT SHALL THE COPYRIGHT
** OWNER OR CONTRIBUTORS BE LIABLE FOR ANY DIRECT, INDIRECT, INCIDENTAL,
** SPECIAL, EXEMPLARY, OR CONSEQUENTIAL DAMAGES (INCLUDING, BUT NOT
** LIMITED TO, PROCUREMENT OF SUBSTITUTE GOODS OR SERVICES; LOSS OF USE,
** DATA, OR PROFITS; OR BUSINESS INTERRUPTION) HOWEVER CAUSED AND ON ANY
** THEORY OF LIABILITY, WHETHER IN CONTRACT, STRICT LIABILITY, OR TORT
** (INCLUDING NEGLIGENCE OR OTHERWISE) ARISING IN ANY WAY OUT OF THE USE
** OF THIS SOFTWARE, EVEN IF ADVISED OF THE POSSIBILITY OF SUCH DAMAGE."
**
** $QT_END_LICENSE$
**
****************************************************************************/

#include <QGuiApplication>
#include <QIcon>
#include <QLoggingCategory>
#include <QQmlApplicationEngine>
#include <QQmlContext>

#include "connectionhandler.h"
#include "devicefinder.h"
#include "devicehandler.h"

int main(int argc, char *argv[])
{
#ifdef BLUETOOTH_DEBUG
    QLoggingCategory::setFilterRules(QStringLiteral("qt.bluetooth* = true"));
#endif
    QGuiApplication app(argc, argv);

    app.setWindowIcon(QIcon(":/qml/images/logo.png"));

    ConnectionHandler connectionHandler;
    DeviceHandler deviceHandler;
    DeviceFinder deviceFinder(&deviceHandler);

    qmlRegisterUncreatableType<DeviceHandler>("Shared", 1, 0, "AddressType", "Enum is not a type");

    QQmlApplicationEngine engine;
    engine.rootContext()->setContextProperty("connectionHandler", &connectionHandler);
    engine.rootContext()->setContextProperty("deviceFinder", &deviceFinder);
    engine.rootContext()->setContextProperty("deviceHandler", &deviceHandler);

    engine.load(QUrl(QStringLiteral("qrc:/qml/main.qml")));

    return app.exec();
}

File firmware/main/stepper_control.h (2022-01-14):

#ifndef STEPPER_CONTROL_H
#define STEPPER_CONTROL_H

#include <cstring>

#if defined(TMC2590)
#include "tmc2590.h"
#elif defined(TMC2160)
#include "tmc2160.h"
#else
#error "No driver selected"
#endif

// Stepper ISR ----------------------------------------------------
// This is the ISR for the timer used for stepping. Note that no
// floating point operations are allowed in ISRs, so they must be
// converted to fixed point by the controller.

// Current position kept track of by the ISR. Output to main thread.
volatile int32_t g_current_position = 0;

// Current direction (1 or -1). Input from main thread.
// This is only used to update g_current_position.
volatile int32_t g_current_dir_sign = 1;

// Whether the next edge should be rising or falling. We use double
// edge stepping (DEDGE=1 in DRVCTRL) to cut down our ISR
// requirements by half. Only used internally in the ISR.
volatile bool g_current_edge = false;

// Semaphore for atomic updates.
portMUX_TYPE g_stepper_timer_mux = portMUX_INITIALIZER_UNLOCKED;

void IRAM_ATTR StepperTimerHandler(void) {
  portENTER_CRITICAL_ISR(&g_stepper_timer_mux);
  digitalWrite(kTmcStep, g_current_edge);
  g_current_edge = !g_current_edge;

  g_current_position += g_current_dir_sign;

  DriverStepHandler();
  portEXIT_CRITICAL_ISR(&g_stepper_timer_mux);
}
// ----------------------------------------------------------------

class MotionController {
 public:
  MotionController();

  void Begin();
  void Stop();

  void SetTargetSpeed(float speed_rps);
  void SetTargetSpeedRPM(float speed_rpm) { SetTargetSpeed(speed_rpm / 60.0f); }

  // Use built-in planner to update target speed to get to target
  // position without overshooting.
  // Note that this class is fundamentally a velocity-based controller,
  // so this convenience function needs to be called before every update to update target 
  // velocity. This is NOT done automatically as part of Update();
  void UpdateTargetSpeedByPosition(int32_t target_position, float max_speed);

  void Update();

  int32_t GetCurrentPosition();
  void SetCurrentPosition(int32_t new_position);
  float GetCurrentSpeed() { return current_speed_; }
  float GetCurrentSpeedRPM() { return current_speed_ * 60.0f; }

  void SetAccelerationLimit(float acceleration_limit) { acceleration_limit_ = acceleration_limit; }
  void SetJerkLimit(float jerk_limit) { jerk_limit_ = jerk_limit; }

  TMCDriver* Driver() { return driver_; }

 private:
  TMCDriver* driver_;
 
  // Speed we are ramping to (Rev/s).
  float target_speed_;

  // Speed we are currently commanding.
  float current_speed_;

  float current_acceleration_;

  float acceleration_limit_;
  float jerk_limit_;

  // Last time the control loop was run.
  uint32_t last_update_time_us_;

  hw_timer_t* step_timer_;
};

MotionController::MotionController()
  : target_speed_(0.0f),
    current_speed_(0.0f),
    current_acceleration_(0.0f),
    acceleration_limit_(kMaxAcceleration),
    jerk_limit_(kMaxJerk),
    last_update_time_us_(0),
    step_timer_(nullptr) {
#if defined(TMC2590)
  driver_ = new TMC2590Driver;
#elif defined(TMC2160)
  driver_ = new TMC2160Driver;
#else
#error "No driver selected"
#endif
}

void MotionController::Begin() {
  driver_->Begin();  
  step_timer_ = timerBegin(3, 80 /* APB_CLK / 80 = 1MHz*/, /*countUp=*/true);
  timerAttachInterrupt(step_timer_, &StepperTimerHandler, 1);
}

void MotionController::Stop() {
  if (step_timer_) {
    timerAlarmDisable(step_timer_);
  }
  driver_->Stop();
}

void MotionController::SetTargetSpeed(float speed_rps) {
  target_speed_ = speed_rps;
}

void MotionController::UpdateTargetSpeedByPosition(
    int32_t target_position, float max_speed) {
  int32_t current_position = GetCurrentPosition();
  
  float position_error = fabs((target_position - current_position) * kRevsPerMicroStep);

  // Given the current position error and our max acceleration,
  // how fast can we be at this point and not overshoot?
  // Note that this calculation ignores jerk limit, so it's not
  // 100% accurate. This also doesn't take into account the current
  // speed (it assumes we are accelerating to the target velocity
  // at infinite acceleration), so it's not optimally efficient.

  // Displacement under constant acceleration is:
  // d = v0 * t + (1/2) * a * t^2
  //
  // d = position_error
  // a = -acceleration_limit_ (assuming v0 > 0, d > 0)
  // t = v0 / -a
  // d = v0 * v0 / -a + (1/2) * a * (v0^2 / a^2)
  //   = -(v0^2 / a) + (1/2) * v0^2 / a
  //   = -(1/2) v0^2 / a
  //   = (1/2) v0^2 / acceleration_limit_
  //
  // |v0| = sqrt(2 * d * acceleration_limit_)

  // TODO: Figure out how we have to drop the 2x to stop overshooting.
  float v_abs = sqrt(position_error * acceleration_limit_);
  float v = 0.0f;

  if (current_position < target_position) {
    v = min(max_speed, v_abs);
  } else {
    v = max(-max_speed, -v_abs);
  }

  SetTargetSpeed(v);
}
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

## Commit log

2021-11-20 Added PCB v1
    [stepper_driver-B_Cu.gbl, stepper_driver-B_Mask.gbs, stepper_driver-B_SilkS.gbo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]
2021-11-24 Simplified control loop and implemented StallGuard thresholds for each direction
    [config.h, main.ino, stepper_control.h]
2021-11-28 Simplified homing procedure
2021-12-06 Implemented direction switching flag, better homing, and tuned max speed/acceleration/jerk
2021-12-20 Hardware design v2 with TMC2160 driver and NEMA 23 form factor for mounting
    [stepper_driver-B_Cu.gbl, stepper_driver-B_Mask.gbs, stepper_driver-B_SilkS.gbo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]
2021-12-23 Added option to control verbose trajctory debug printing
2021-12-23 Reverted control loop to 200Hz
    [main.ino]
2021-12-23 Added fix for potential delay time overflow
    [config.h, stepper_control.h]
2021-12-24 Refactored TMC driver to support alternative IC, and improved low speed / idling
2021-12-29 Refactored homing controller out into own class, and started TMC2160 driver
2021-12-29 Removed stray manufacturing files
    [stepper_driver_bom_jlc.csv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]
2021-12-30 Minor board updates
    [stepper_driver.kicad_pcb, stepper_driver.sch]
2021-12-30 Finished basic impl of TMC2160 driver
2022-01-02 Updated schematics and PCB doc
2022-01-02 Added more fet driver tuning for TMC2160
2022-01-14 Optimised 2160 gate driver config
2022-01-14 Updated hardware to rev 3
    [stepper_driver.kicad_pcb, stepper_driver.sch]
2022-01-14 Implemented latching stall detection for TMC2160
    [stepper_control.h, tmc2160.h, tmc2590.h]
2022-01-15 Improved board revision handling
2022-01-15 Rev3 PCB tweaks
    [stepper_driver.kicad_pcb, stepper_driver.sch]
2022-01-15 Board documentation re-org
2022-01-15 Added PNG schematics
2022-01-15 Cosmetics update
    [stepper_driver.kicad_pcb, stepper_driver.sch]
2022-01-18 Finalised rev3 files
    [stepper_driver-B_Cu.gbl, stepper_driver-B_Mask.gbs, stepper_driver-B_SilkS.gbo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]
2022-01-18 Minor PCB cleanup and updated tline analysis
    [stepper_driver.kicad_pcb]
2022-02-02 Added firmware support for rev3 board
2022-02-02 Added spacer for NEMA 23 stepper + rev 3 board
    [stepper_spacer.3mf, stepper_spacer.f3d]
